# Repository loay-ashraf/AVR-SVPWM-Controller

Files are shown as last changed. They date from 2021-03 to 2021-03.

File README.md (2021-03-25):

# AVR SVPWM Controller
SVPWM controller prototype implemented using AVR 8-bit microcontroller as a part of EV car conversion graduation project for Mechatronics Engineering Bachelor - Fall 2018.

## Overview
This section gives an overview of the system.

### Concept
Space vector pulse width modulation (SVPWM) is an algorithm for the control of pulse width modulation (PWM).

It is used for the creation of alternating current (AC) waveforms; most commonly to drive 3 phase AC powered motors at varying speeds from DC using multiple MOSFET/IGBT transistors. 

### System Layout
System is divided into two separate modules that communicate with each other to acheive the desired output, which are:

#### Pilot Module

Pilot module receives operating parameters from co-pilot (output frequency) and then outputs PWM signals to IGBT bridge, also it checks for current fault signal and in case of current overload it shuts down waiting for a manual reset.

#### Co-Pilot Module

Co-Pilot module reads user input via rotary potentiometer for output frequency, current sensor for current overload signal, then sends operating parameters to Pilot module and finally outputs system status (frequency, RPM, current,...etc.) to a character LCD.

## Discussion
This section discusses desicions made regarding design and implementation.

### Microcontroller

1. We opted for ATmega128 for pilot module as it runs at 16MHZ frequency and also has two 16-bit timers each having three output compare pins.
2. We opted for ATmega32 for co-pilot module as it runs at 16MHZ frequency and has enough pins for interfacing character LCD and current sensors via ADC.

### Communication Protocol

It is found that best communcation type (protocol) for such system would be a parallel communication bus because of the following reasons:

- Distance between modules is so short (<5m)
- Data sent is time senstive
- Pilot module is starving for CPU clock cycles to calculate and update timer's compare registers values and going with parallel would be ideal for this situation as it only costs one CPU clock cycle to read PINx register 

So we opted for an 8-bit wide parallel communication bus (including READY and ACK signals) which would be much faster than any serial communication available (USART, I2C and SPI).

### Timer Mode

We used Phase and Frequency correct PWM mode with ICR1 as TOP value as it mimics the center aligned PWM mode required for the space vector algorithm.

## Sample Output

### Non-Filtered Output

Below is the ouput of the system without attaching low pass LC filter:

SVPWM non-filtered

### Filtered Output

Below is the output of the system with low pass LC filter attached:

SVPWM filtered

## Built With
- Atmel Studio 7 - The official AVR IDE
- AVR-gcc V5.4 - C compiler
- GNU Make - auto-generated makefile
- CadSoft EAGLE - PCB design tool

## Authors
Loay Ashraf - <loay.ashraf.96@gmail.com>

Mohamed Gamal - <muhammed.gamal051@gmail.com>

## License
This project is licensed under the MIT License - see the LICENSE.md file for details

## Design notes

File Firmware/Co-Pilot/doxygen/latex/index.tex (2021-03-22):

\begin{DoxyAuthor}{Author}
Loay Ashraf \href{mailto:loay.ashraf.96@gmail.com}{\tt loay.\+ashraf.\+96@gmail.\+com} 
\end{DoxyAuthor}
\begin{DoxyVersion}{Version}
1.\+0.\+0
\end{DoxyVersion}
This program processes and shows current inverter status like Voltage, Frequency and the speed of the motor and sets the main controller output by communicating via parallel bus using 8-\/bit data line, one A\+CK line and one R\+E\+A\+DY line; It also interfaces 16x2 parallel interface L\+CD.

\begin{DoxyParagraph}{Pin Assignments\+: }

\begin{DoxyItemize}
\item P\+A0\+: Speed Potentiometer signal
\item P\+A1-\/3\+: Phases current signal
\item P\+B0-\/3\+: L\+CD 4-\/bit Data signal
\item P\+B5\+: L\+CD EN signal
\item P\+B6\+: L\+CD RS signal
\item P\+B7\+: Direction Data signal
\item P\+C0-\/7\+: Parallel bus 8-\/bit Data signal
\item P\+D0-\/1\+: Direction Switch signal
\item P\+D3\+: Current Overload signal
\item P\+D5\+: Parallel bus R\+E\+A\+DY signal
\item P\+D6\+: Parallel bus A\+CK signal 
\end{DoxyItemize}
\end{DoxyParagraph}

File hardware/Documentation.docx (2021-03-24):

# T5 pure sine wave inverter

# T5.1 Circuit diagram

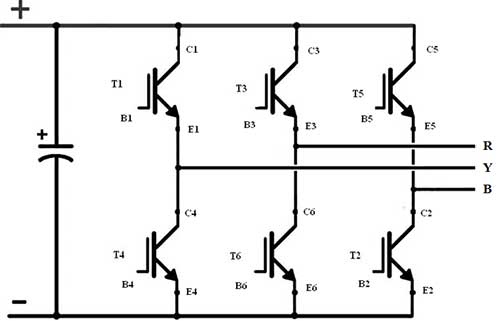
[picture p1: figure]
Description: circuit-diagram-of-three-phase-inverter

The basic circuit of inverter consists of 6 IGBTs connected like this diagram to produce 3-phase system every phase consists of 2 IGBTs each one has phase shift 180 degree which we call for example high side at 0 degree and low side for 180 degree the high side transistor is responsible for generating the positive side of the wave and the low side is responsible for generating the negative side of the wave .Each transistor of the high side has phase shift 120 degree from the next transistor and each transistor of the low side has 120 degree from the next transistor for example: the first phase high side has 0 degree; the second has 120 degree and the 240 degree and the same for low side.

T5.2 Components

T5.2.1 IGBT

The reason of using IGBT neither MOSFET nor BJT isn’t only because the high current and voltage rating but also it has their advantages like high current sensitivity at gate like BJT and high voltage sensitivity at gain like MOSFET.

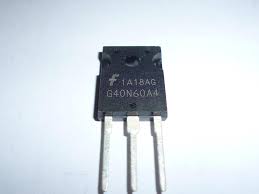
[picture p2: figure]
Description: Image result for igbt g40n60

Fig. IGBT

T5.2.2 Optocoupler driver

The purpose of optocoupler driver is to drive the IGBT gate and isolate the power signal from the control signal in order to protect the power signal from the noise.

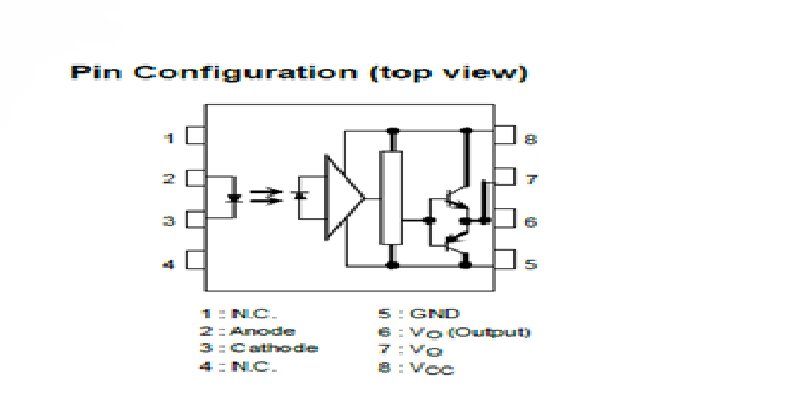
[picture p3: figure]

Fig. optocoupler driver

These are the main components of the main inverter circuit and now let us see the actual inverter circuit you may notice few differences from the basic circuit like the resistors and the capacitors each one has purpose like the 10k ohm resistor between the optocoupler output and the IGBT gate and the 330 ohm at the signal output in the Molex to reduce the amps ,the 10 ohm between the gate and the emitter to prevent parasitic turn on via miller capacitance stray inductance, and the capacitors connected to the driver to work as a filter for the rebels and the noise.

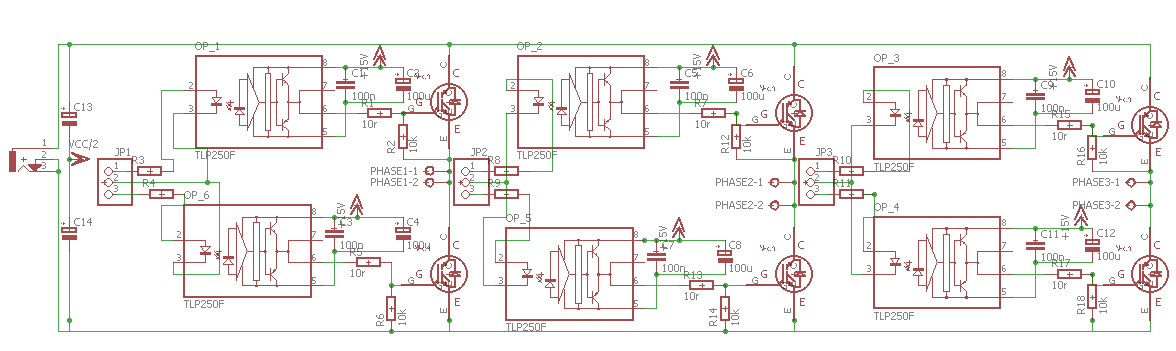
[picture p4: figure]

Fig. The actual inverter circuit

The layout

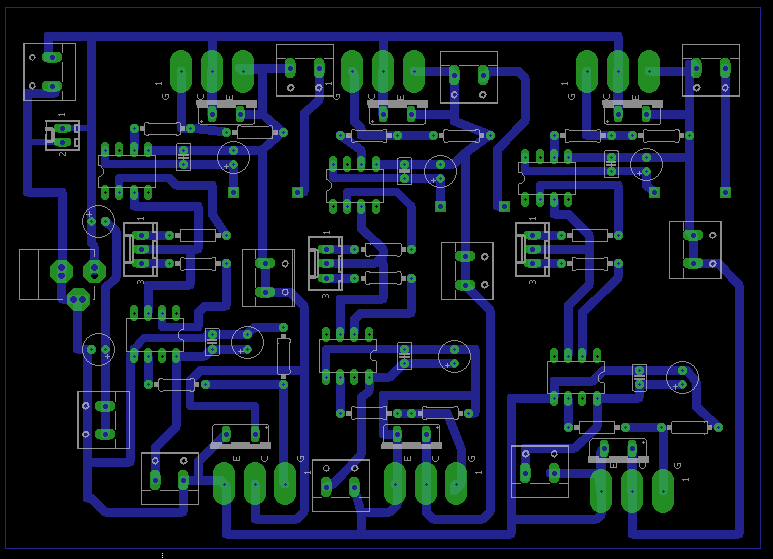
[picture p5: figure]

T5.3 pilot circuit

The pilot circuit is needed to operate and control the inverter output and here the circuit segments in this circuit we used in this circuit ATmega128 because it has two 16-bit timers (Timer1, Timer3), with each timer having 3 output compare units and also can operate in Phase and Frequency Correct (Center-Aligned PWM) mode which is enough for SVPWM signal generation.

T5.3.1 Power supply

The input voltage ranges from 12 to 9 volts the diode is used as a protection method from wrong connection, the 100Uf capacitors are used to reduce the rebels in the supply volt, the 100nF capacitors are used to eliminate the noise from other circuits, the regulator is used to produce 5v from the supply and the led is used as an indicator of the supply.

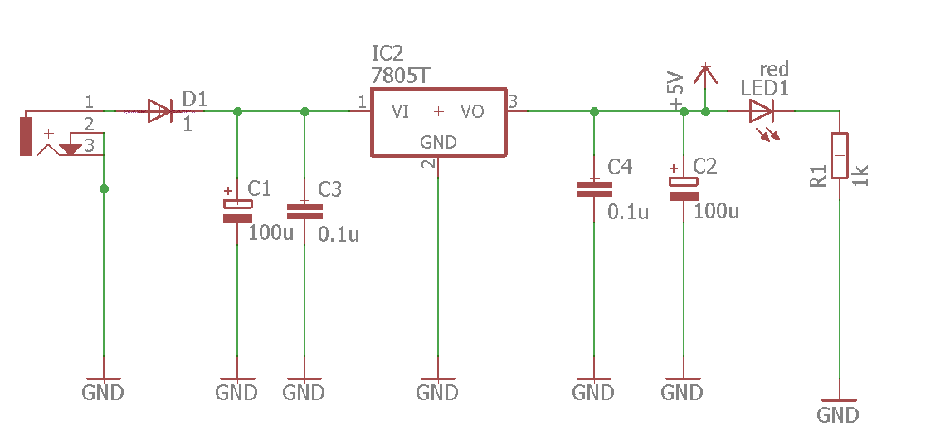
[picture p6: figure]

T5.3.2 Reset circuit

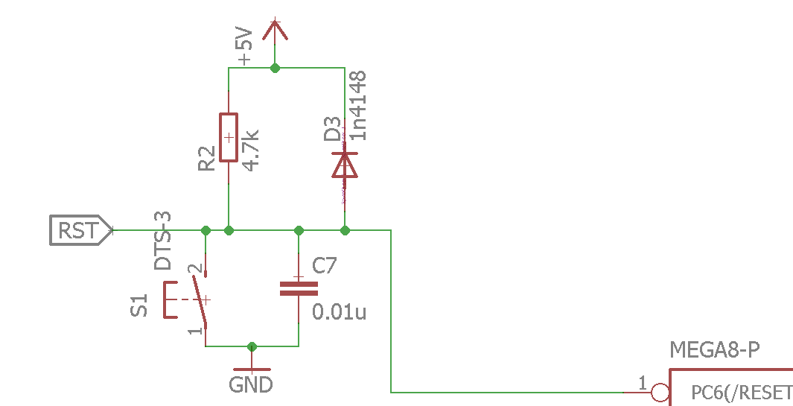
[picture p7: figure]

This circuit is the recommended reset circuit from Atmel.

T5.3.3 Isp programming port

T5.3.4 Logic circuits and Molex

1-not gate

2- Schmitt trigger

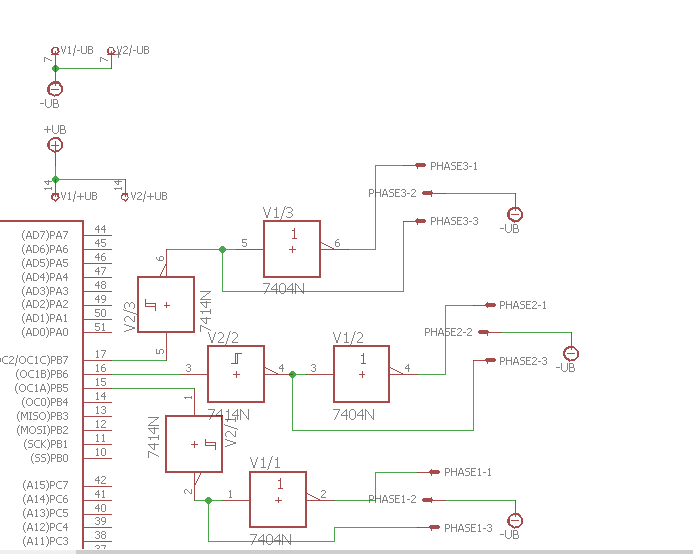
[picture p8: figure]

Fig. Schmitt trigger

The not gate is needed to make the phase shift 180-degree between the high and the low side of each phase the Schmitt trigger is used to make the output increase to a steady max value when the input is between 5v and 2 v and decrease to almost zero when the input is lower than 2, and the 3 pins Molex as output interface between the controller and the inverter circuit.

T5.3.5 Clock circuit

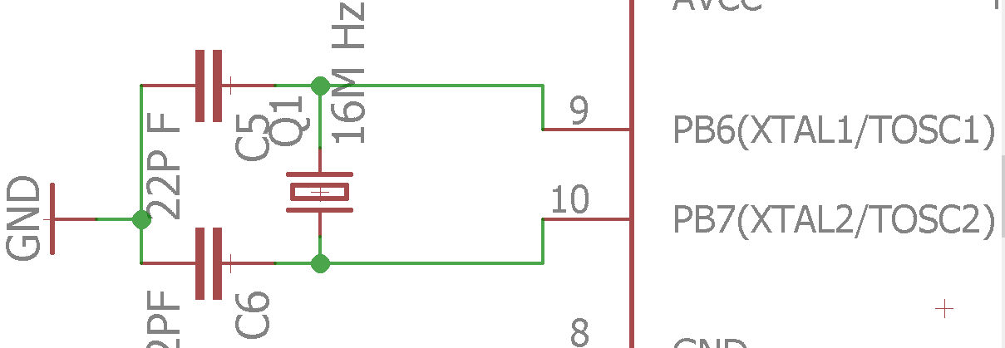
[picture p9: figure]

The 22 pF capacitors are needed to reduce the resonance at the start of the cycle

T5.3.6 Data port

The data port is needed to transfer the data collected from the co-pilot circuit which we need to vary the inverter speed, it consists of 8-bit parallel communication port to receive procced data from the co -pilot, acknowledge as confirmation flag between the co-pilot and the pilot, ready to initiate new data transfer , direction pin which indicates the direction of the motor, RST which is master reset pin between the two controllers and of course the positive and negative rail of the circuit.

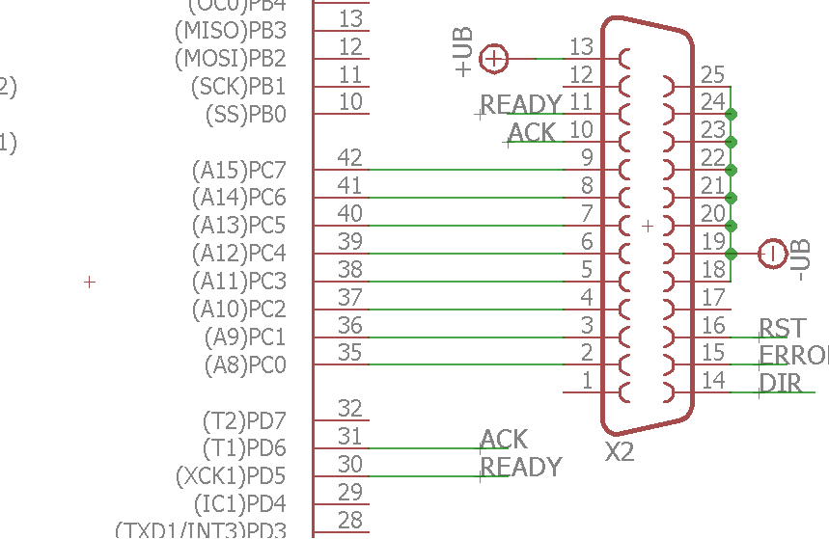
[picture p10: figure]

Full circuit diagram

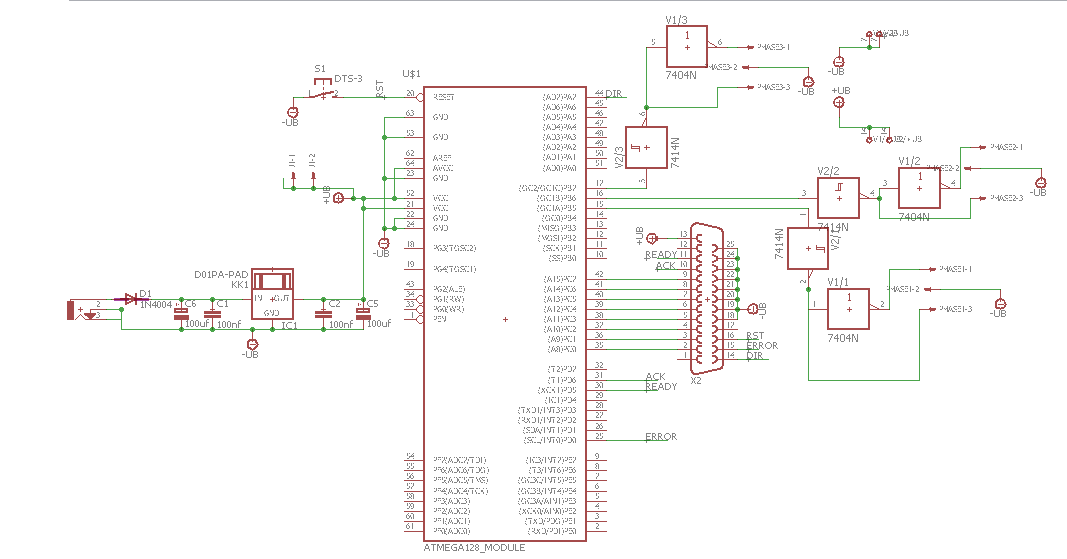
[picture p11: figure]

The layout

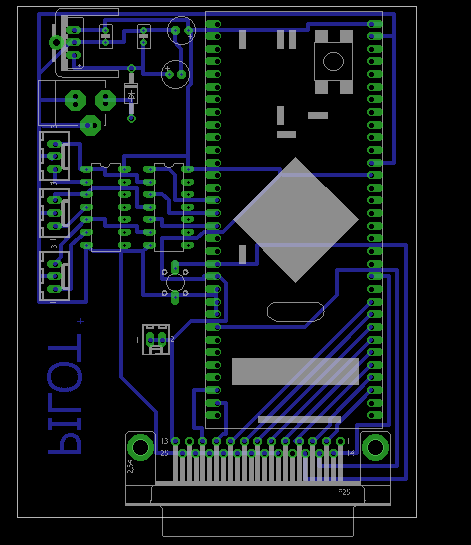
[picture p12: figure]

T5.4 co-pilot circuit

The purpose of the co-pilot circuit is to transform the analog signal from the potentiometer into digital value stored in one single port and display the output of the inverter on LCD for this circuit we have chosen ATmega32 due to presence of large program memory size, SRAM size and number of I/O pins.

1- Clock

The clock circuit is the same like the previous circuit.

2-Data port

The same like the last circuit except that this circuit is the one which transmits the data.

3-Pedals interface

The interface between the circuit and the pedal is 3 pins one; connected to ground, one to V_(cc) and the last one in the middle is connected to ADC pin in microcontroller.

4-Direction interface

We use 3 position switch to display the 3 states of the motor clockwise direction, anti-clockwise direction and stop.

5-LCD Display

We use 16*2-character LCD to display voltage, frequency and speed.

Full circuit diagram

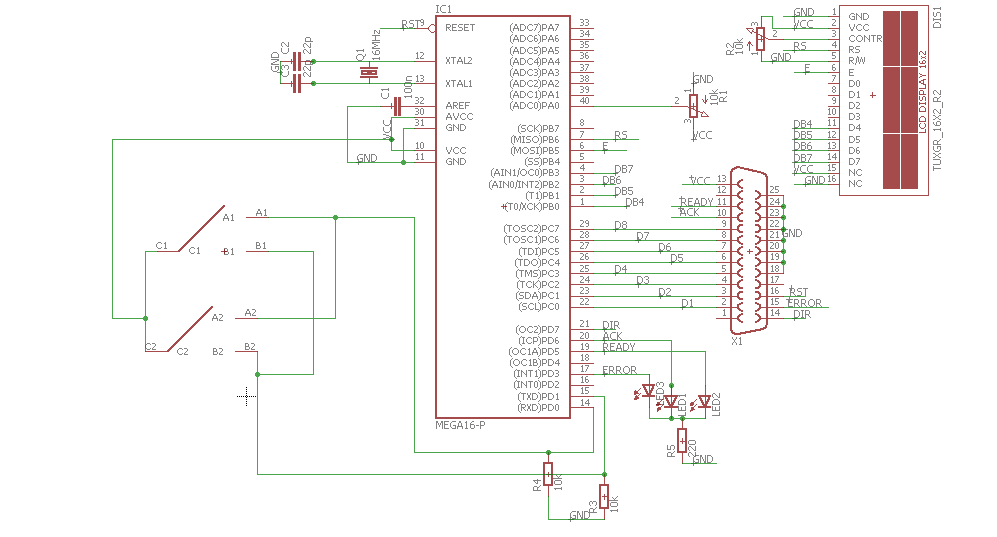
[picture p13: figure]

The layout

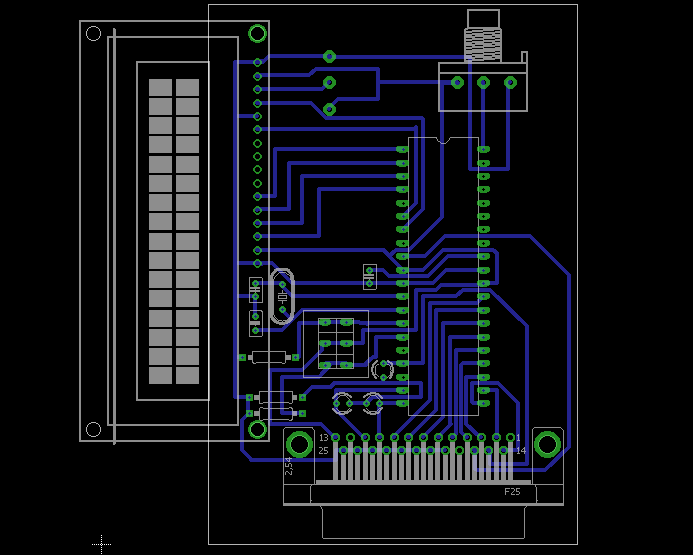
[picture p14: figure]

T5.5 DC filter

We know from the datasheet of the IGBT that the voltage level needed to open the gate is 15 V so the use of dc filter is to reduce the voltage levels difference between sources so the IGBT gates will open simultaneously. We use four dc filters one for the low side transistors and one for each transistor of the high side.

Circuit diagram

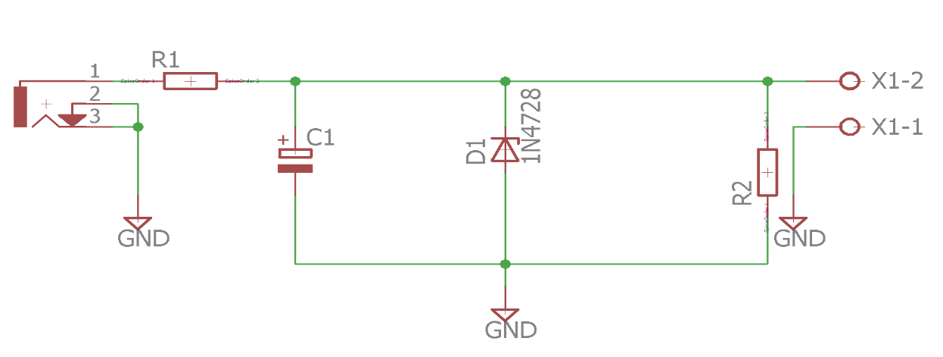
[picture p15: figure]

The layout

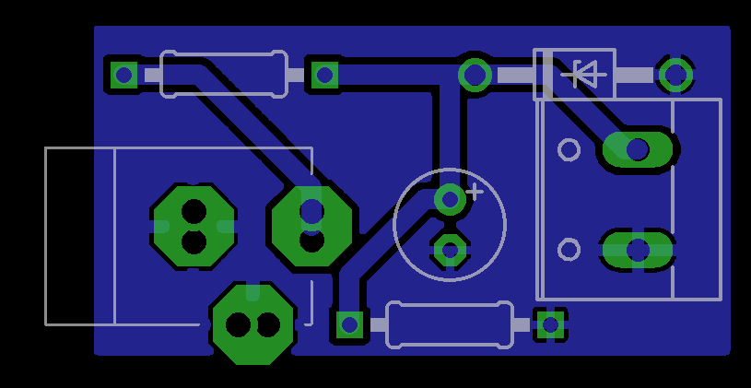
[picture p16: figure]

T5.6 LC Filter circuit

It is known that the output of the inverter is a square wave but we need sinusoidal wave so we need low pass filter circuit like LC filter which consists of inductor reactance and capacitor impulse on the inverter and motor terminals

The values of the capacitor and the inductor is given by

f_c =1/(π√(LC))

Where

f_c is the cut off frequency in hertz

π is mathematical π =3.14

L is the inductance in Henry

C is the capacitance in Farad

For this study case the frequency from the MCU is 7000 HZ

In order to get rid of switching harmonics (up to tenth harmonic)

the cut off frequency of the filter has to be (at most) 700HZ

the available inductance in the market value is 150 u Henry

so, the needed capacitance is 374 u Farad but due to lack of such value in the market we used 8 capacitors each capacitor is 47uFarad for each phase.

Yet such filter will not be able to sustain sine wave shape under every loading condition so a damper circuit is needed.

Circuit diagram

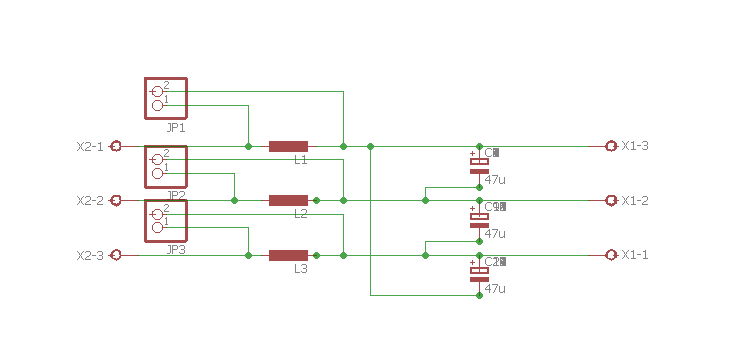
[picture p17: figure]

The layout

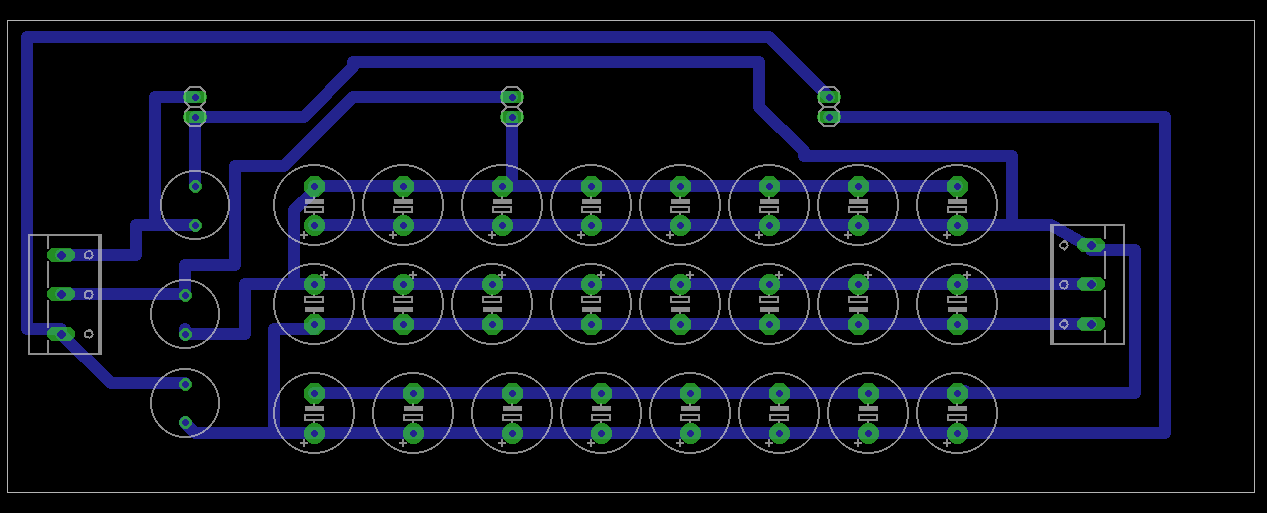
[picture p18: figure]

T5.7 Damper circuit

The presence of dumper eliminates any occasional ringing of output form and helps stabilizes its faster.

There are two kinds of damper

1- series damper:

it consists of a resistor connected in series with inductor and this arrangement is connected parallel with LC filter inductor.

Rd=sqrt(L/C)

Ld=n*L

WHERE n =2/15

2-parallel Damper:

it consists of a resistor connected in series with Capacitor and this arrangement is connected parallel with LC filter Capacitor.

Rd=sqrt(L/C)

Cd=n*C

WHERE n =4

We used in our circuit series damper because the value of the required inductor value is easier to obtain more than the required capacitor in case of parallel damper.

So:

Rd=0.63 ohm

Ld= 20u Henry

Circuit diagram

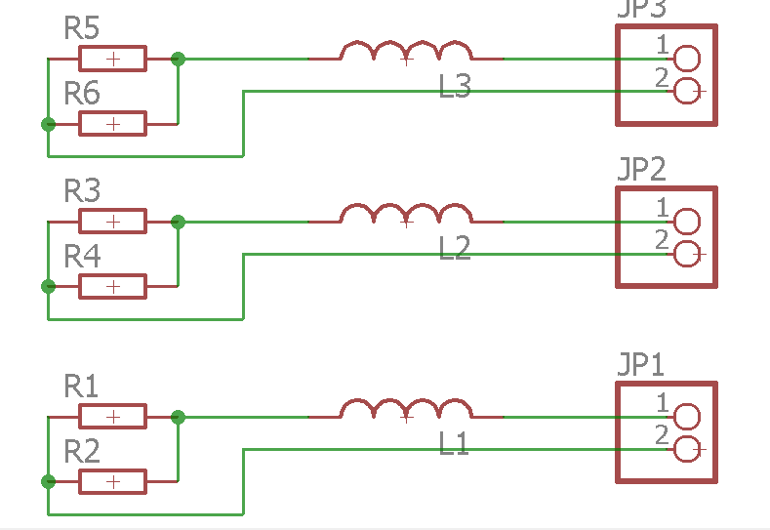
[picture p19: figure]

The layout

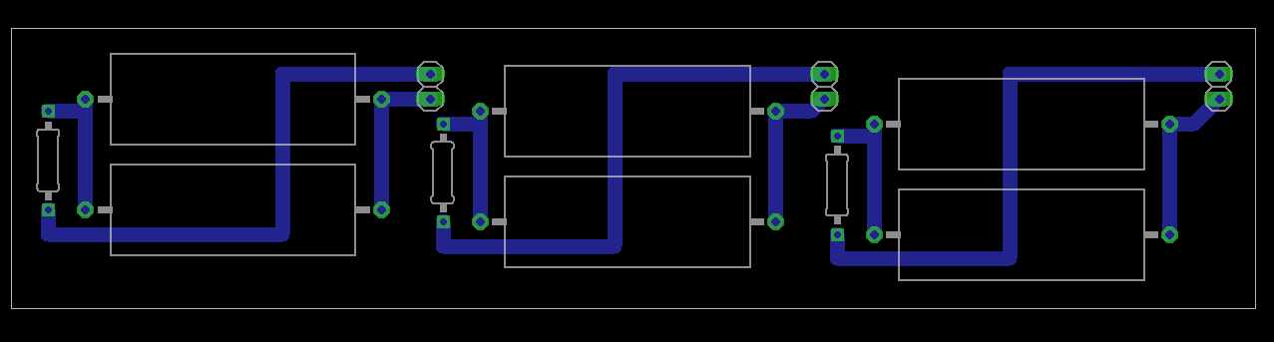
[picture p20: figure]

T6 Excel sheet for inverter calculations

This sheet is used to calculate the amp of the motor as the power and voltage is given &to insert the frequency to be used in further equations.

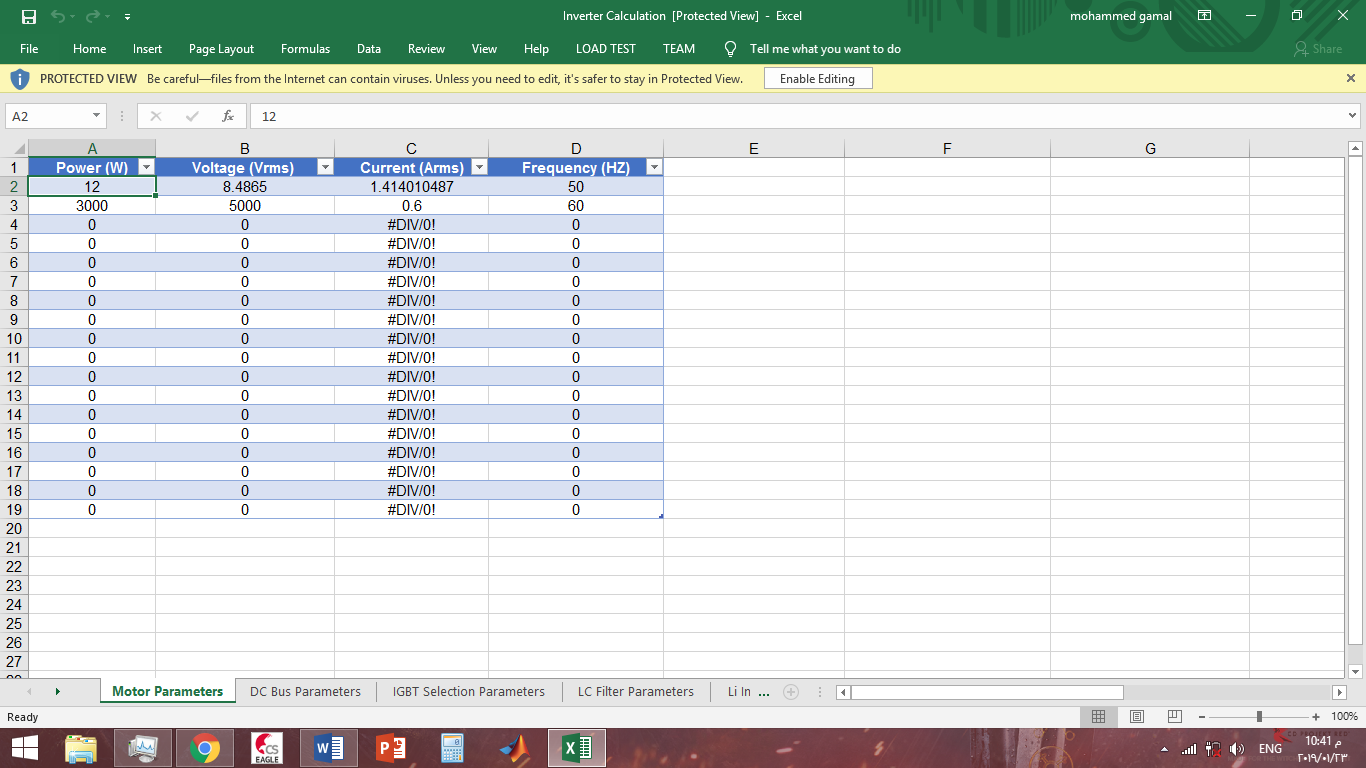
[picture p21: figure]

This sheet is used to calculate both the voltage and amp as rms value

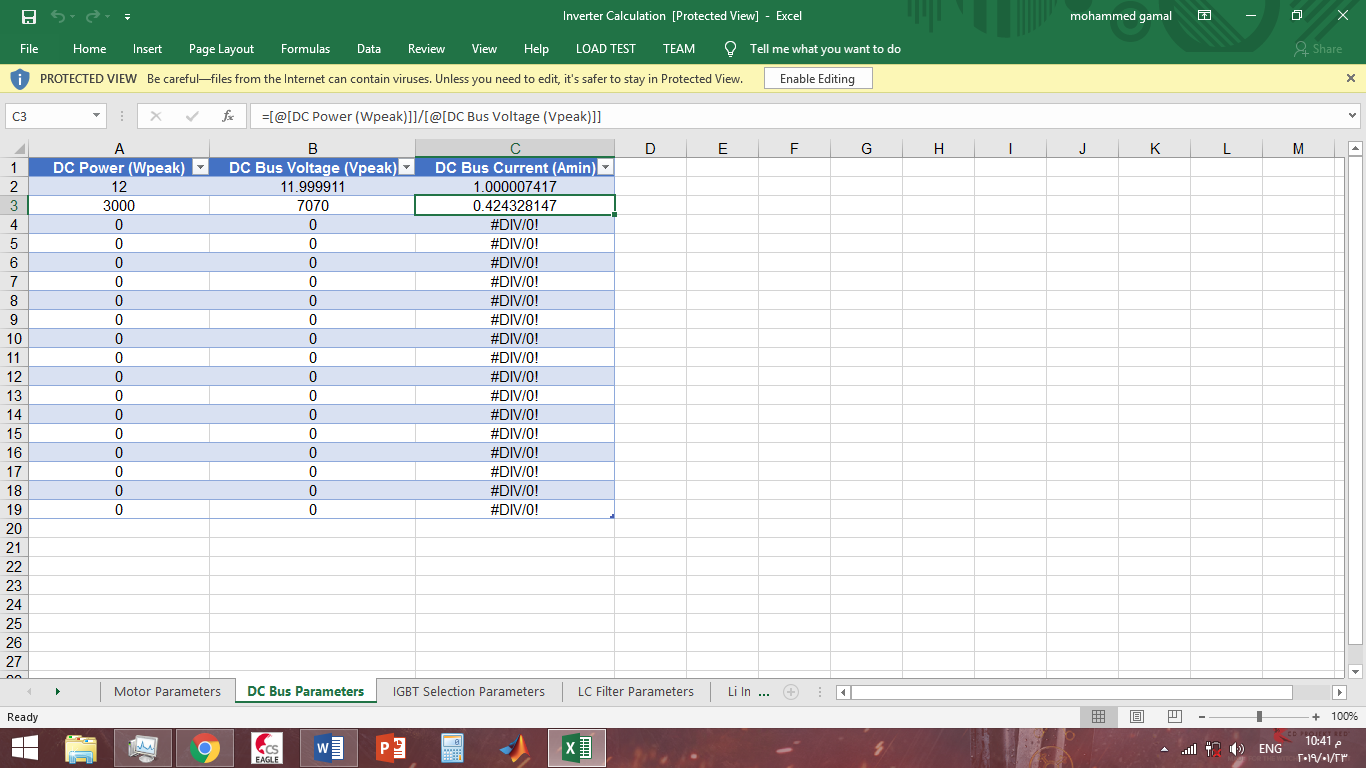
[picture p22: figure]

This sheet to calculate the parameter on which we has chosen the IGBT used in the inverter circuit.

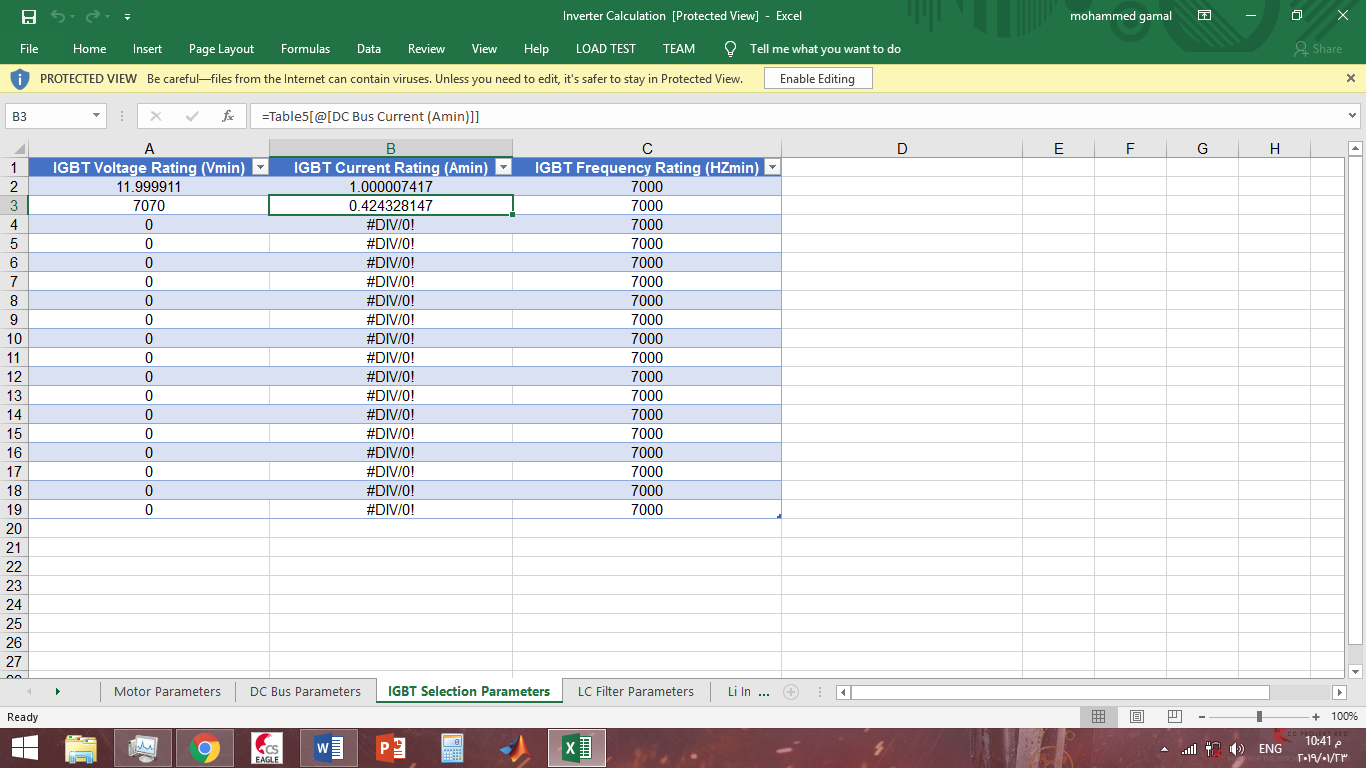
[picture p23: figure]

In this sheet we calculated the parameters of the LC filter and its damper we select reactive power parentage and current ripple due to the application.

This sheet is used to calculate the number of turns for the toroid inductor base on the available core dimensions and the calculated inductance from the previous sheet.

T7 MATLAB simulation

in case of basis inverter, no filter applied

we see that the output is square wave.

in case of inverter with LC filter without the damper

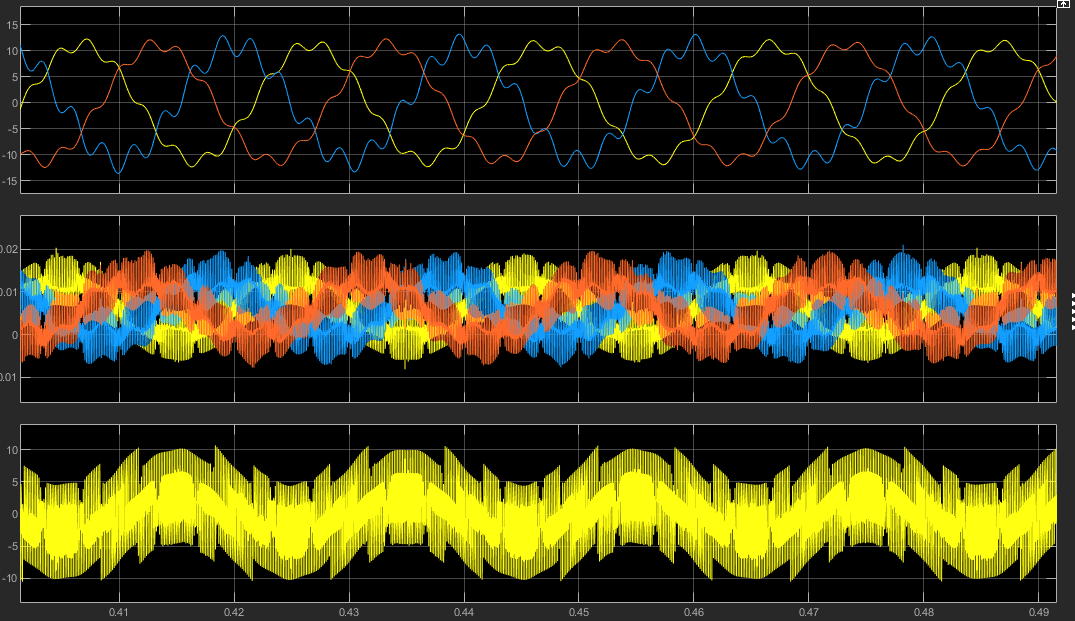
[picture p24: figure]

the wave form takes time to stabilize and even after stabilization the occasional ringing of output form which presents sin wave but with ripples on the peak of the wave.

in case of the inverter with filter and damper

we note the occasional ringing of output form is eliminated and the wave form is stable and presents pure sin wave from the start even on high loads.

T8 the advantages of Pure Sine-wave inverters

-The output waveform is a sine-wave with very low harmonic distortion and clean power like utility supplied electricity

-Inductive loads like microwaves and motors run faster, quieter and cooler

-Reduces audible and electrical noise in fans, fluorescent lights, audio amplifiers, TV, fax and answering machines

-Prevents crashes in computers, weird print outs and glitches in monitors

Electric Vehicle conversion- Graduation Project Mechatronics department, Faculty of Engineering Mansoura University

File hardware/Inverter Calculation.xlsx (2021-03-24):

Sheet: Motor Parameters
Power (W) | Voltage (Vrms) | Current (Arms) | Frequency (HZ)
12 | 8.4865 | 1.414010487 | 50
3000 | 5000 | 0.6 | 60
0 | 0 | #DIV/0! | 0
0 | 0 | #DIV/0! | 0
0 | 0 | #DIV/0! | 0
0 | 0 | #DIV/0! | 0
0 | 0 | #DIV/0! | 0
0 | 0 | #DIV/0! | 0
0 | 0 | #DIV/0! | 0
0 | 0 | #DIV/0! | 0
0 | 0 | #DIV/0! | 0
0 | 0 | #DIV/0! | 0
0 | 0 | #DIV/0! | 0
0 | 0 | #DIV/0! | 0
0 | 0 | #DIV/0! | 0
0 | 0 | #DIV/0! | 0
0 | 0 | #DIV/0! | 0
0 | 0 | #DIV/0! | 0

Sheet: DC Bus Parameters
DC Power (Wpeak) | DC Bus Voltage (Vpeak) | DC Bus Current (Amin)
12 | 11.999911 | 1.000007417
3000 | 7070 | 0.4243281471
0 | 0 | #DIV/0!
0 | 0 | #DIV/0!
0 | 0 | #DIV/0!
0 | 0 | #DIV/0!
0 | 0 | #DIV/0!
0 | 0 | #DIV/0!
0 | 0 | #DIV/0!
0 | 0 | #DIV/0!
0 | 0 | #DIV/0!
0 | 0 | #DIV/0!
0 | 0 | #DIV/0!
0 | 0 | #DIV/0!
0 | 0 | #DIV/0!
0 | 0 | #DIV/0!
0 | 0 | #DIV/0!
0 | 0 | #DIV/0!
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

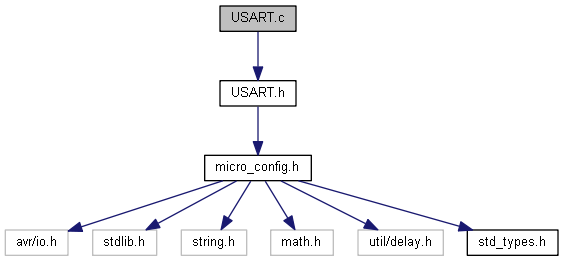
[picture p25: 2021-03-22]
Firmware/Co-Pilot/doxygen/_u_s_a_r_t_8c__incl.png

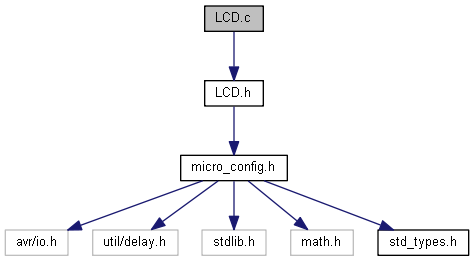
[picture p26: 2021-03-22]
Firmware/Co-Pilot/doxygen/_l_c_d_8c__incl.png

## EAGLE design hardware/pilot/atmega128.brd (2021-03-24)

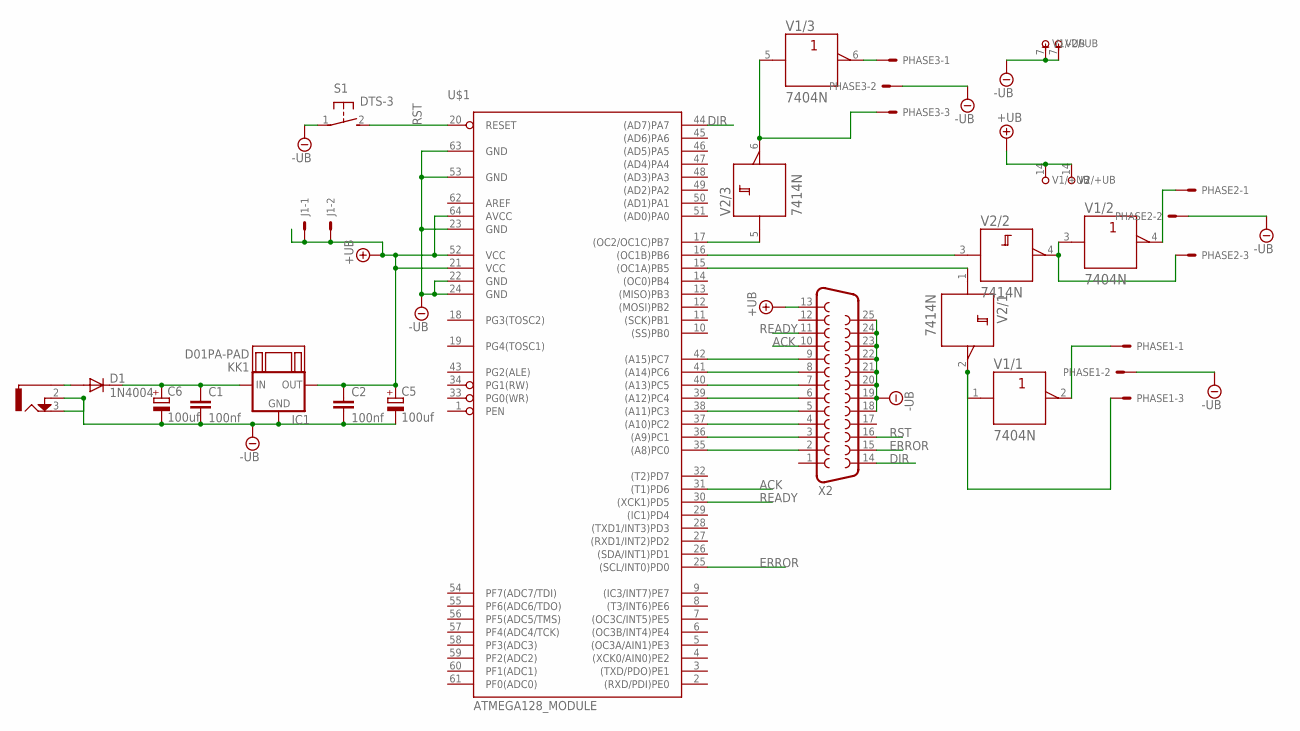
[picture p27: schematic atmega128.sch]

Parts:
C1, C2: 100nf; C025-025X050
C5, C6: 100uf; E2,5-6
D1: 1N4004; DO41-10
IC1: 78XXS
J1: 22-27-2021-02; 6410-02
KK1: D01PA-PAD
PHASE1, PHASE2, PHASE3: 6410-03
S1: DTS-3
U$1: ATMEGA128_MODULE
U$2: DC-21MM
V1: 7404N; DIL14
V2: 7414N; DIL14
X2: F25HP

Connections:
+UB: C2.1, C5.+, IC1.OUT, J1.1, J1.2, U$1.21 (VCC), U$1.52 (VCC), U$1.64 (AVCC), V1.14 (+UB), V2.14 (+UB), X2.13
-UB: C1.2, C2.2, C5.-, C6.-, IC1.GND, PHASE1.2, PHASE2.2, PHASE3.2, S1.1, U$1.22 (GND), U$1.23 (GND), U$1.24 (GND), U$1.53 (GND), U$1.63 (GND), U$2.2, U$2.3, V1.7 (-UB), V2.7 (-UB), X2.18, X2.19, X2.20, X2.21, X2.22, X2.23, X2.24, X2.25
ACK: U$1.31 ((T1)PD6), X2.10
DIR: U$1.44 ((AD7)PA7), X2.14
ERROR: U$1.25 ((SCL/INT0)PD0), X2.15
unnamed: D1.A, U$2.1
unnamed: C1.1, C6.+, D1.C, IC1.IN
unnamed: U$1.42 ((A15)PC7), X2.9
unnamed: U$1.41 ((A14)PC6), X2.8
unnamed: U$1.40 ((A13)PC5), X2.7
unnamed: U$1.39 ((A12)PC4), X2.6
unnamed: U$1.38 ((A11)PC3), X2.5
unnamed: U$1.37 ((A10)PC2), X2.4
unnamed: U$1.36 ((A9)PC1), X2.3
unnamed: U$1.35 ((A8)PC0), X2.2
PHASE1: U$1.15 ((OC1A)PB5), V2.1 (A)
PHASE1HIGH: PHASE1.1, V1.2 (Y)
PHASE1LOW: PHASE1.3, V1.1 (A), V2.2 (Y)
PHASE2: U$1.16 ((OC1B)PB6), V2.3 (A)
PHASE2HIGH: PHASE2.1, V1.4 (Y)
PHASE2LOW: PHASE2.3, V1.3 (A), V2.4 (Y)
PHASE3: U$1.17 ((OC2/OC1C)PB7), V2.5 (A)
PHASE3HIGH: PHASE3.1, V1.6 (Y)
PHASE3LOW: PHASE3.3, V1.5 (A), V2.6 (Y)
READY: U$1.30 ((XCK1)PD5), X2.11
RST: S1.2, U$1.20 (RESET), X2.16

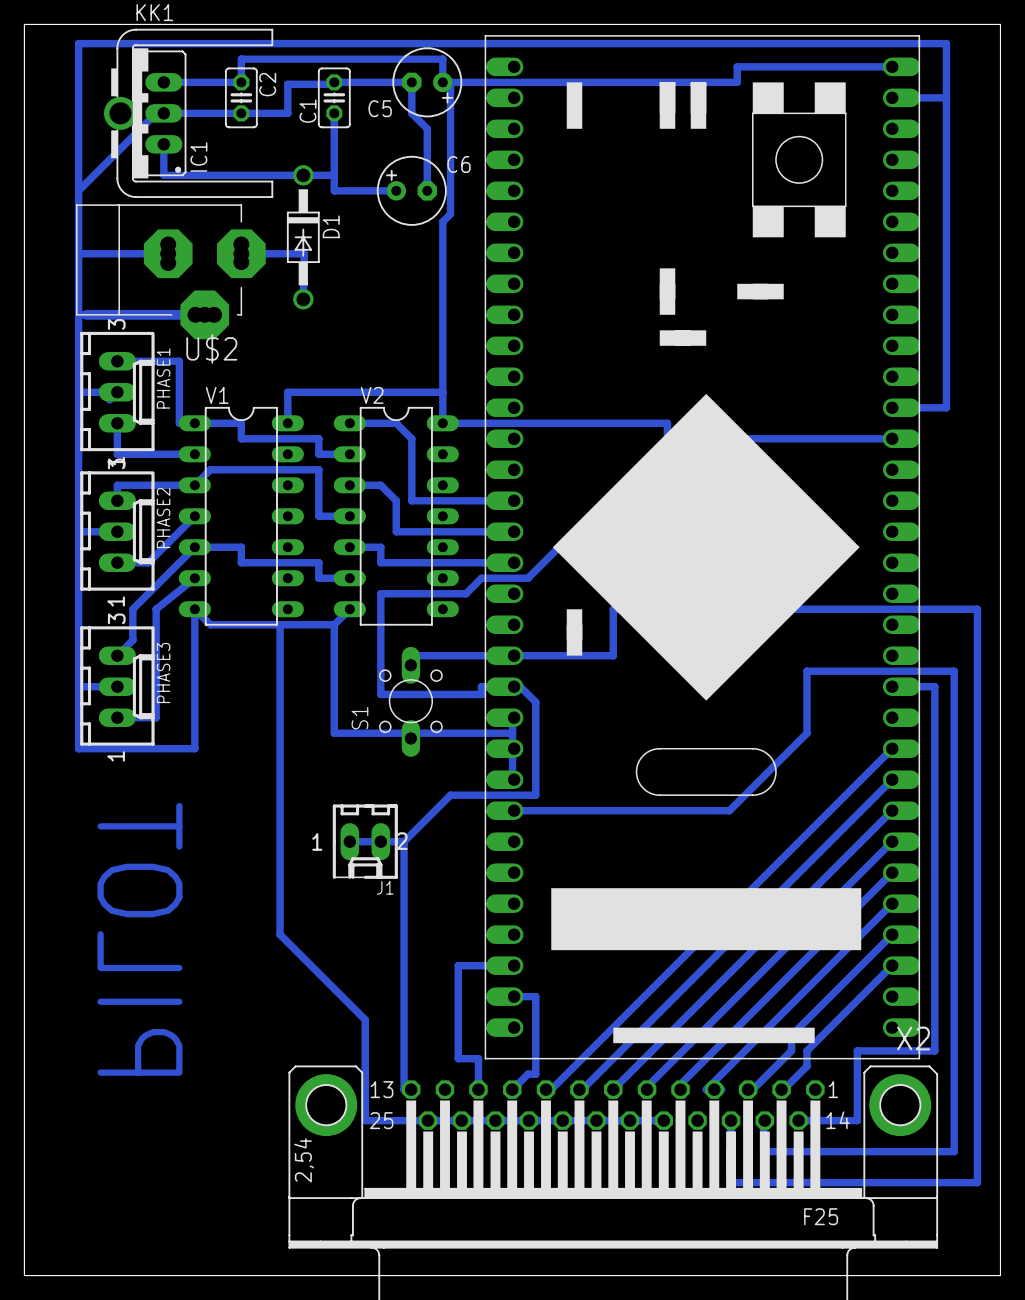
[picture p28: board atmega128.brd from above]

Board: 2 copper layers, 80.0 x 102.5 mm, 17 parts (0 on the bottom side), 26 nets.

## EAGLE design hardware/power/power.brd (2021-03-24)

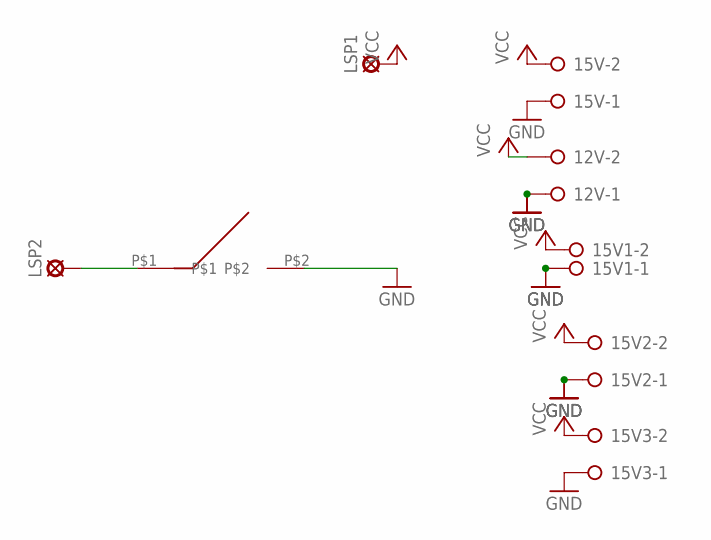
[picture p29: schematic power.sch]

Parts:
12V, 15V, 15V1, 15V2, 15V3: W237-02P; W237-132
LSP1, LSP2: SE14
U$1: ON/OFF

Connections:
GND: 12V.1, 15V.1, 15V1.1, 15V2.1, 15V3.1, U$1.P$2
unnamed: LSP2.MP, U$1.P$1
VCC: 12V.2, 15V.2, 15V1.2, 15V2.2, 15V3.2, LSP1.MP

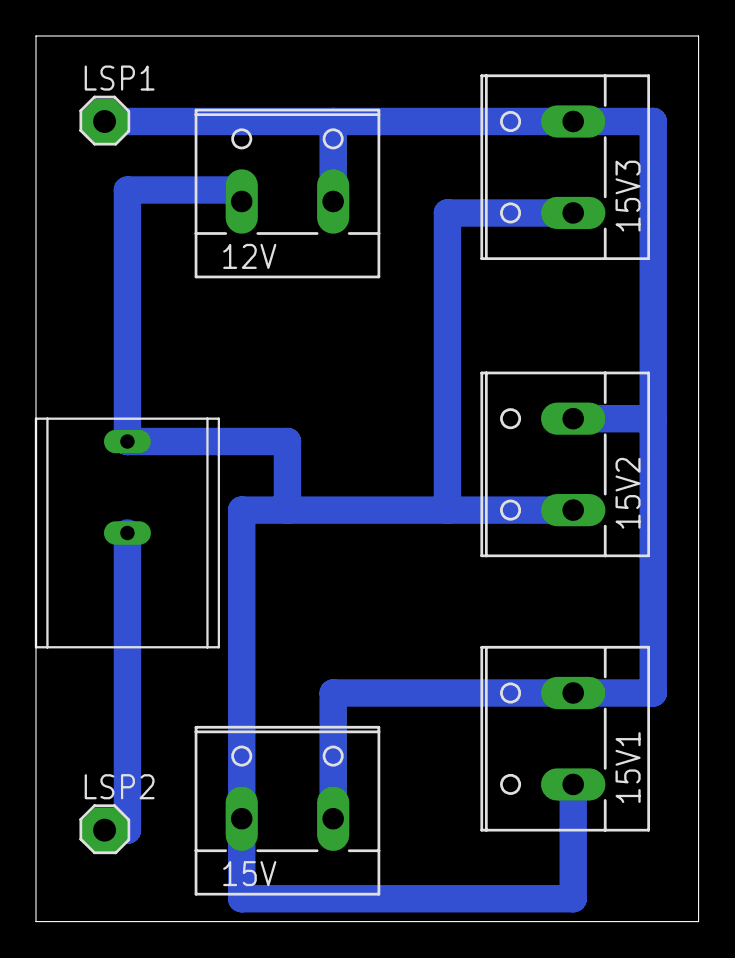
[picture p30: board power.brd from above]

Board: 2 copper layers, 36.8 x 49.2 mm, 8 parts (0 on the bottom side), 3 nets.

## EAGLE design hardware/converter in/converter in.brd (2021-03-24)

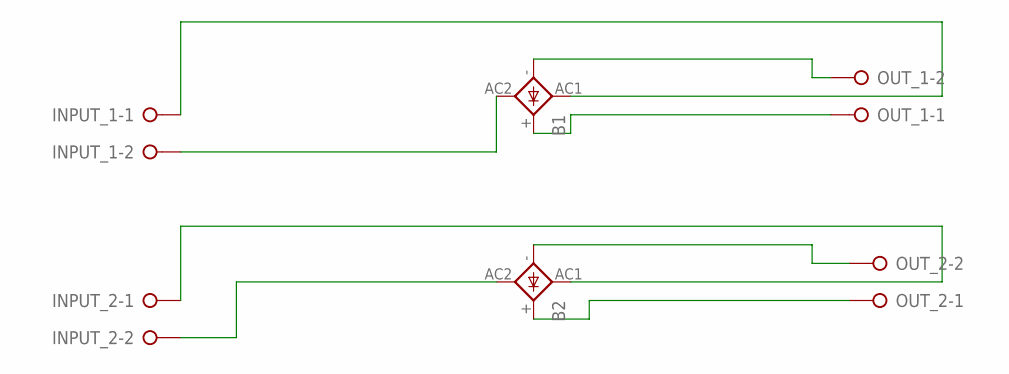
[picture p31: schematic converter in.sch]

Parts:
B1, B2: 2KBP
INPUT_1, INPUT_2: W237-02P; W237-132
OUT_1, OUT_2: W237-02P; W237-132

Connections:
unnamed: B1.-, OUT_1.2
unnamed: B1.+, OUT_1.1
unnamed: B2.-, OUT_2.2
unnamed: B2.+, OUT_2.1
unnamed: B2.AC1, INPUT_2.1
unnamed: B2.AC2, INPUT_2.2
unnamed: B1.AC2, INPUT_1.2
unnamed: B1.AC1, INPUT_1.1

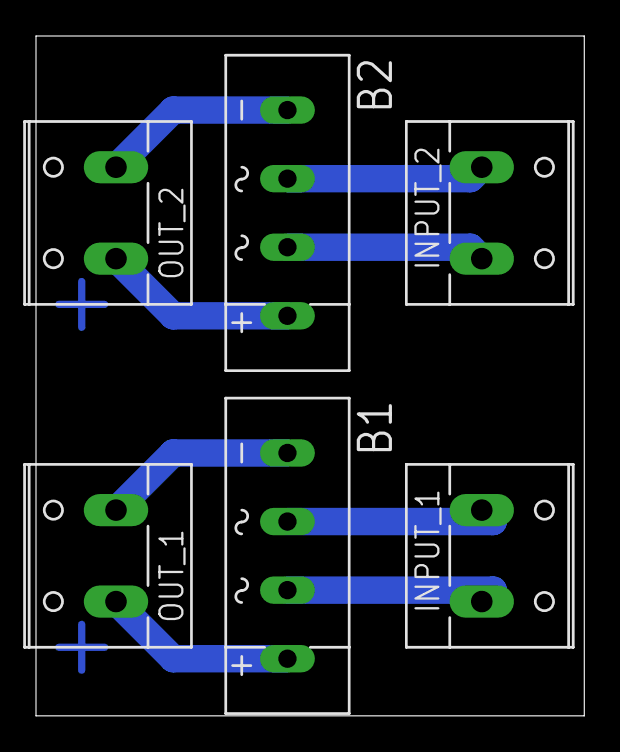
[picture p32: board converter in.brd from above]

Board: 2 copper layers, 30.5 x 37.8 mm, 6 parts (0 on the bottom side), 8 nets.

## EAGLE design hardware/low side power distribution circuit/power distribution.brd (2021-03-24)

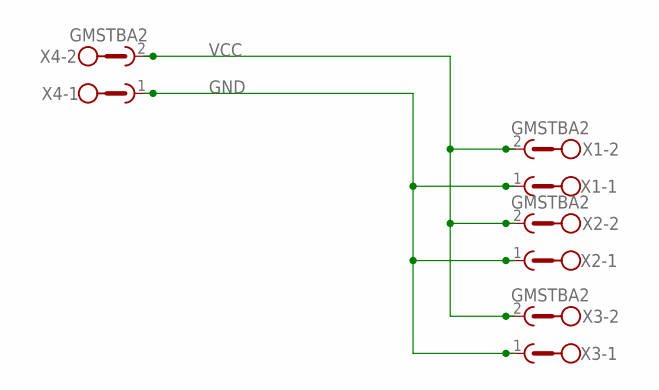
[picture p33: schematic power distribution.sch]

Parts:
X1, X2, X3, X4: GMSTBA2

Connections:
GND: X1.1, X2.1, X3.1, X4.1
VCC: X1.2, X2.2, X3.2, X4.2

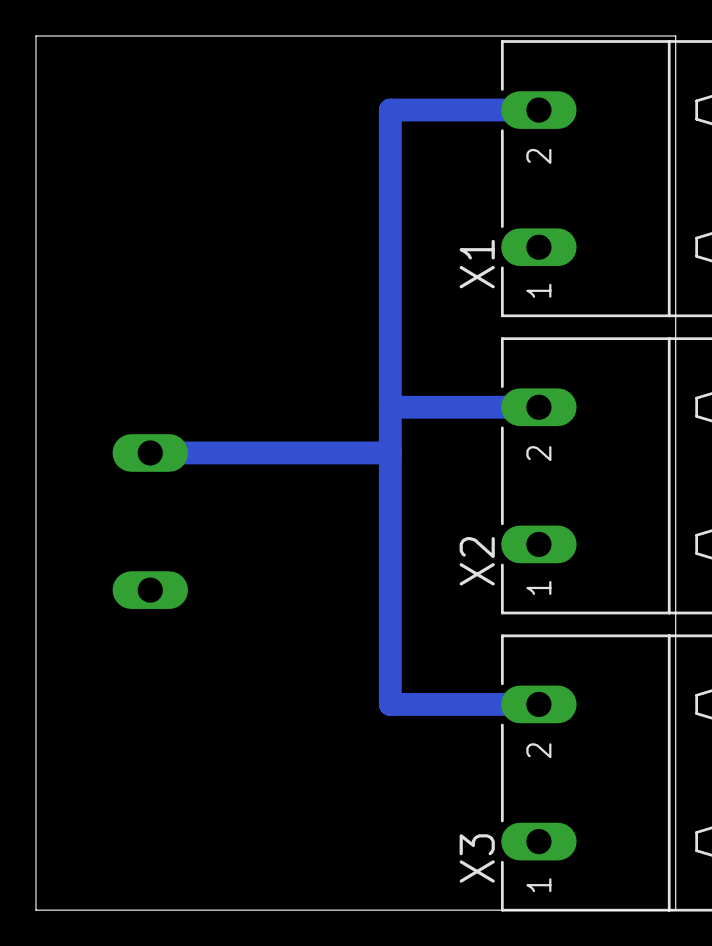
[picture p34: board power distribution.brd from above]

Board: 2 copper layers, 35.5 x 48.6 mm, 4 parts (1 on the bottom side), 2 nets.

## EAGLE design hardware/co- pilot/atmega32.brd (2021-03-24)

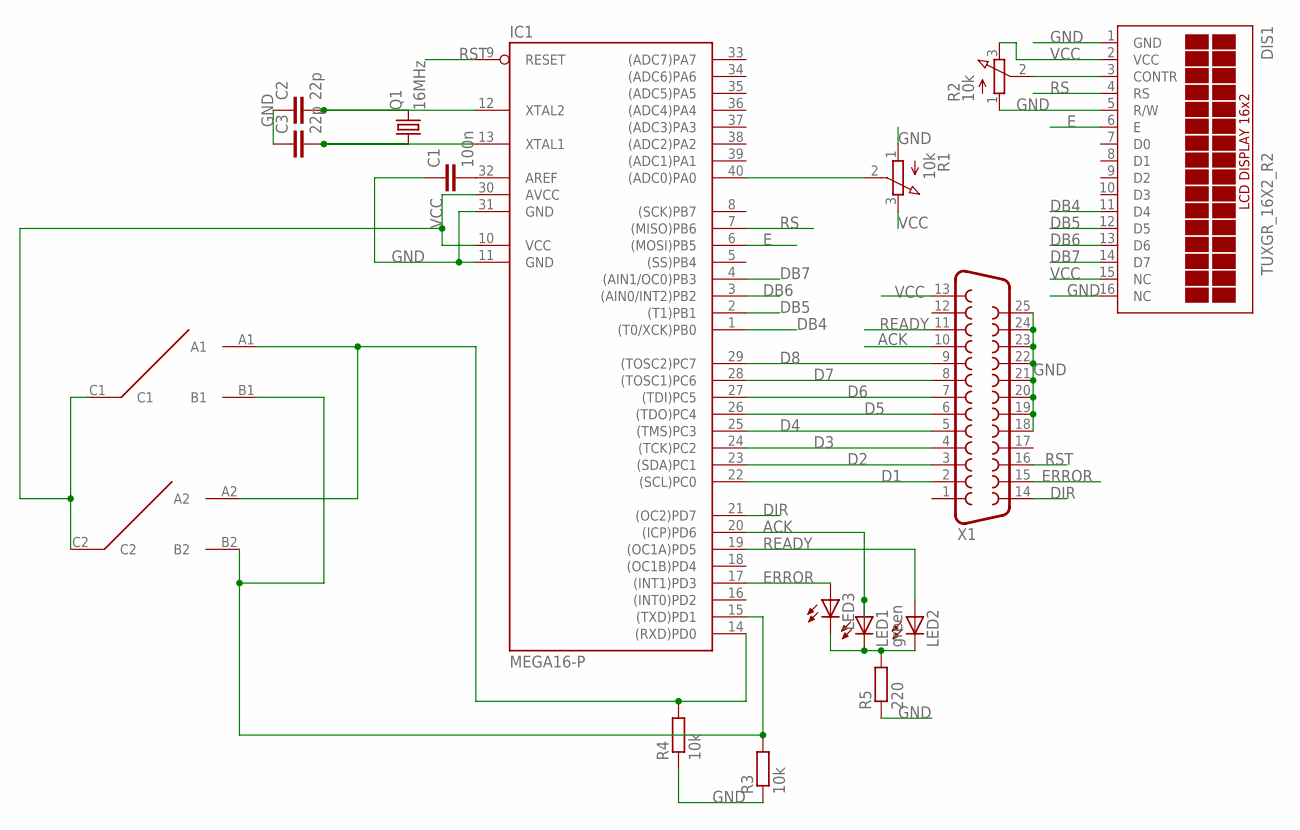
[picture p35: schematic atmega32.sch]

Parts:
C1: 100n; C025-025X050
C2, C3: 22p; C025-025X050
DIS1: TUXGR_16X2_R2
IC1: MEGA16-P; DIL40
LED1: green; LED3MM
LED2, LED3: LED3MM
Q1: 16MHz; HC49/S
R1, R2: 10k; 3RP/1610N
R3, R4: 10k; 0207/10
R5: 220; 0207/10
U$1: TOGGLE
X1: F25HP

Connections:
ACK: IC1.20 ((ICP)PD6), LED1.A, X1.10
D1: IC1.22 ((SCL)PC0), X1.2
D2: IC1.23 ((SDA)PC1), X1.3
D3: IC1.24 ((TCK)PC2), X1.4
D4: IC1.25 ((TMS)PC3), X1.5
D5: IC1.26 ((TDO)PC4), X1.6
D6: IC1.27 ((TDI)PC5), X1.7
D7: IC1.28 ((TOSC1)PC6), X1.8
D8: IC1.29 ((TOSC2)PC7), X1.9
DB4: DIS1.11 (D4), IC1.1 ((T0/XCK)PB0)
DB5: DIS1.12 (D5), IC1.2 ((T1)PB1)
DB6: DIS1.13 (D6), IC1.3 ((AIN0/INT2)PB2)
DB7: DIS1.14 (D7), IC1.4 ((AIN1/OC0)PB3)
DIR: IC1.21 ((OC2)PD7), X1.14
E: DIS1.6 (E), IC1.6 ((MOSI)PB5)
ERROR: IC1.17 ((INT1)PD3), LED3.A, X1.15
GND: C1.1, C2.1, C3.1, DIS1.1 (GND), DIS1.5 (R/W), DIS1.16 (NC), IC1.11 (GND), IC1.31 (GND), R1.1 (A), R2.1 (A), R3.1, R4.1, R5.1, X1.18, X1.19, X1.20, X1.21, X1.22, X1.23, X1.24, X1.25
unnamed: LED1.K (C), LED2.K (C), LED3.K (C), R5.2
unnamed: IC1.14 ((RXD)PD0), R4.2, U$1.A1, U$1.A2
unnamed: IC1.15 ((TXD)PD1), R3.2, U$1.B1, U$1.B2
unnamed: C2.2, IC1.12 (XTAL2), Q1.2
unnamed: IC1.40 ((ADC0)PA0), R1.2 (S)
unnamed: C1.2, IC1.32 (AREF)
unnamed: C3.2, IC1.13 (XTAL1), Q1.1
unnamed: DIS1.3 (CONTR), R2.2 (S)
READY: IC1.19 ((OC1A)PD5), LED2.A, X1.11
RS: DIS1.4 (RS), IC1.7 ((MISO)PB6)
RST: IC1.9 (RESET), X1.16
VCC: DIS1.2 (VCC), DIS1.15 (NC), IC1.10 (VCC), IC1.30 (AVCC), R1.3 (E), R2.3 (E), U$1.C1, U$1.C2, X1.13

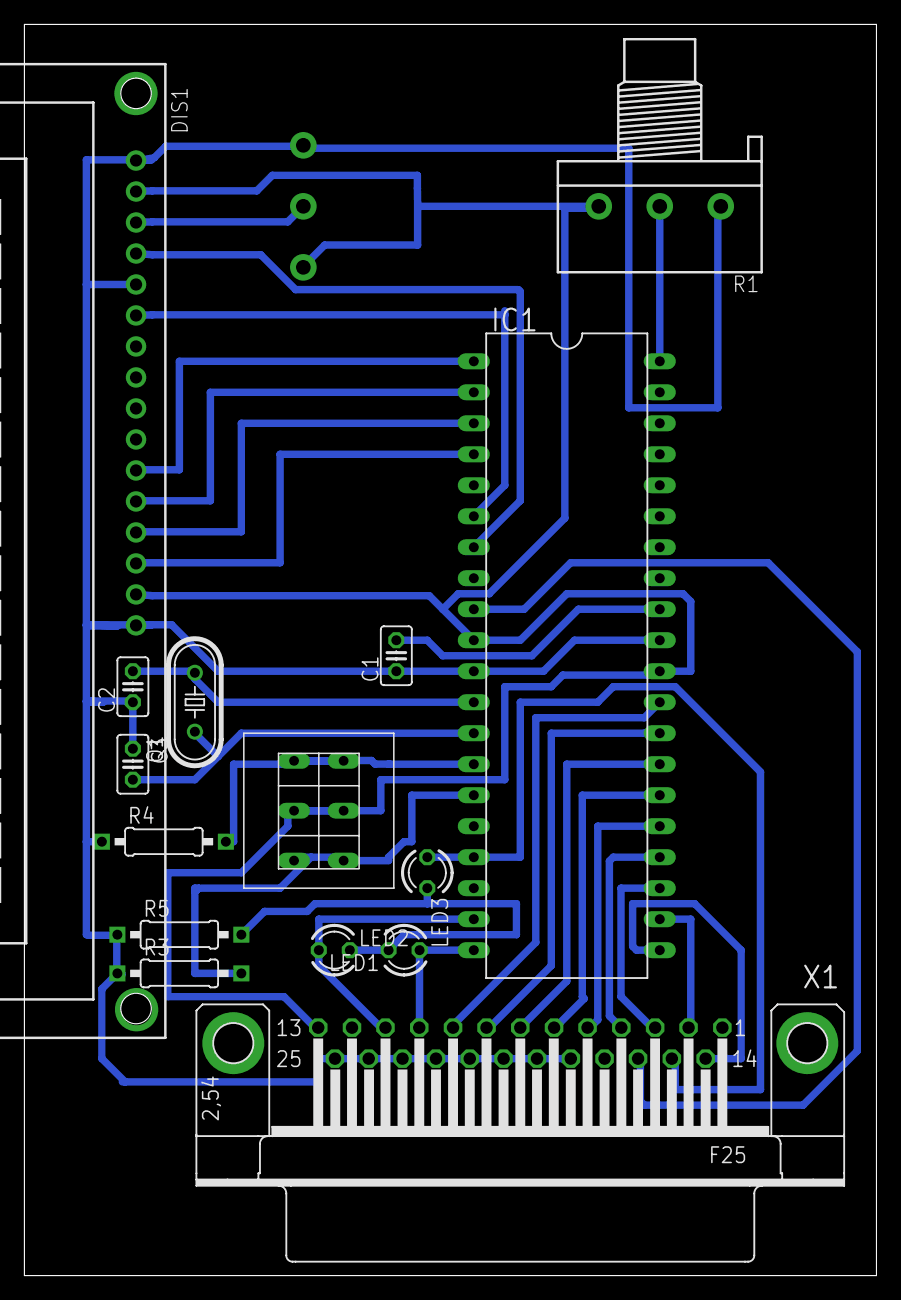
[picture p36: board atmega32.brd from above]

Board: 2 copper layers, 69.8 x 102.5 mm, 16 parts (1 on the bottom side), 29 nets.

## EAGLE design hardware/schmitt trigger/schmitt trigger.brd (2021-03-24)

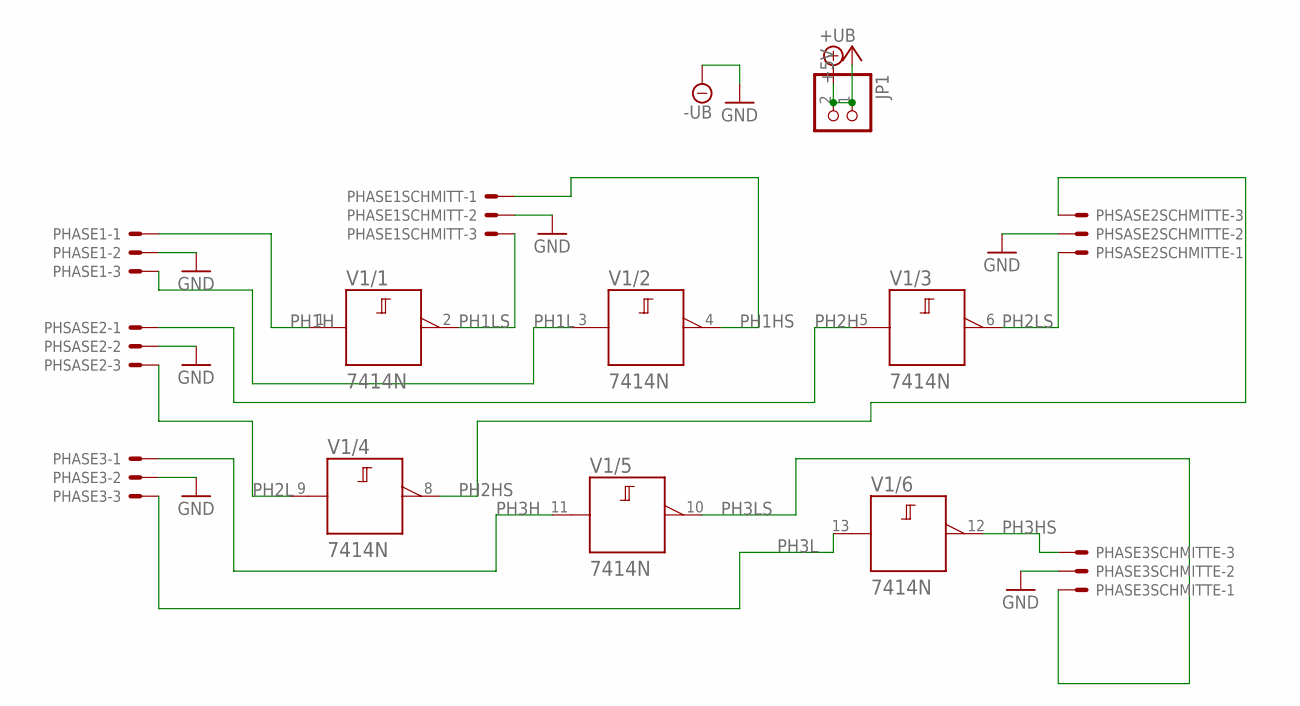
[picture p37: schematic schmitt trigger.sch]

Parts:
JP1: PINHD-1X2; 1X02
PHASE1, PHASE1SCHMITT, PHASE3, PHASE3SCHMITTE: 22-23-2031
PHSASE2, PHSASE2SCHMITTE: 22-23-2031
V1: 7414N; DIL14

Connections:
+5V: JP1.1, JP1.2, V1.14 (+UB)
GND: PHASE1.2, PHASE1SCHMITT.2, PHASE3.2, PHASE3SCHMITTE.2, PHSASE2.2, PHSASE2SCHMITTE.2, V1.7 (-UB)
PH1H: PHASE1.1, V1.1 (A)
PH1HS: PHASE1SCHMITT.1, V1.4 (Y)
PH1L: PHASE1.3, V1.3 (A)
PH1LS: PHASE1SCHMITT.3, V1.2 (Y)
PH2H: PHSASE2.1, V1.5 (A)
PH2HS: PHSASE2SCHMITTE.3, V1.8 (Y)
PH2L: PHSASE2.3, V1.9 (A)
PH2LS: PHSASE2SCHMITTE.1, V1.6 (Y)
PH3H: PHASE3.1, V1.11 (A)
PH3HS: PHASE3SCHMITTE.3, V1.12 (Y)
PH3L: PHASE3.3, V1.13 (A)
PH3LS: PHASE3SCHMITTE.1, V1.10 (Y)

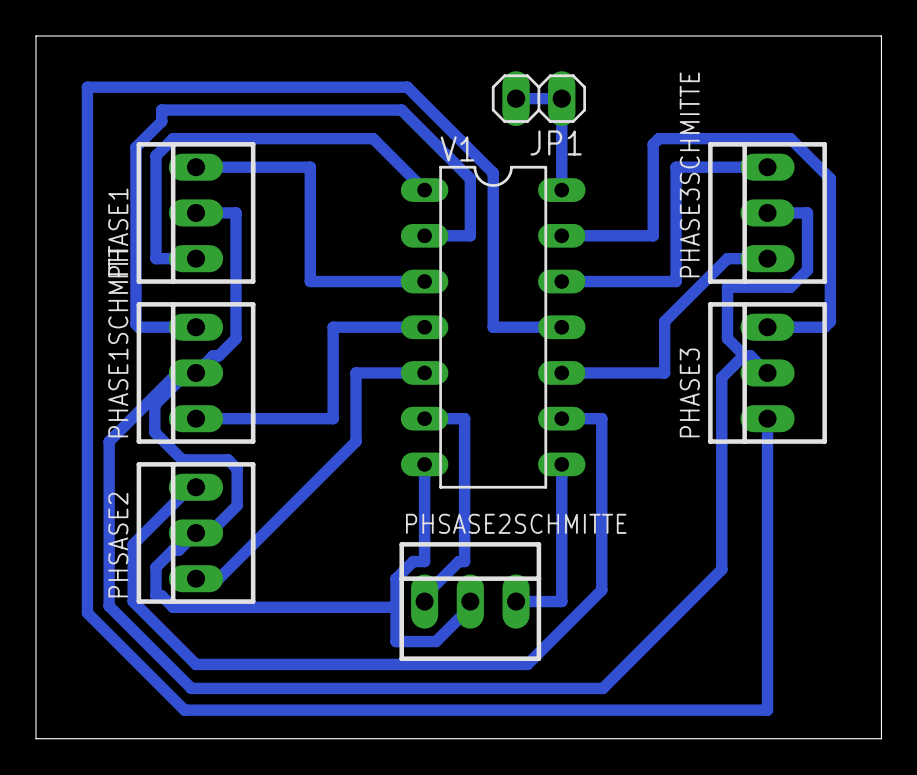
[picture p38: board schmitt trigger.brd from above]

Board: 2 copper layers, 47.0 x 39.0 mm, 8 parts (0 on the bottom side), 14 nets.

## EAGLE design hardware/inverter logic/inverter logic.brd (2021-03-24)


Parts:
C1, C3, C5, C7, C9, C11: 100n; C025-025X050
C2, C4, C6, C8, C10, C12: 100u; E2,5-6
C13, C14: CPOL-EUE2.5-6; E2,5-6
D1, D2, D3, D4, D5, D6: BYW29; DO220S
DRIVE_LOW, DRIVE_LOW1, DRIVE_LOW2: W237-02P; W237-132
DRIVE_SOURCE1, DRIVE_SOURCE2, DRIVE_SOURCE3: W237-02P; W237-132
J1: 22-27-2021-02; 6410-02
OP_1, OP_2, OP_3, OP_4, OP_5, OP_6: TLP250F; DIL08
PHASE1, PHASE2: 22-27-2031-03; 6410-03
PHSASE3: 22-27-2031-03; 6410-03
POWER: W237-02P; W237-132
R1, R3, R5, R7, R9, R11: 10R; 0207/10
R2, R4, R6, R8, R10, R12: 10K; 0207/10
RH1, RH2, RH3: 330; 0207/10
RL1, RL2, RL3: 330; 0207/10
T1, T2, T3, T4, T5, T6: TO-247A; TO-247
U$1: DC-21MM
X1, X2, X3, X4: W237-02P; W237-132

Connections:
+15V: C7.1, C8.+, C9.1, C10.+, C11.1, C12.+, DRIVE_LOW.1, DRIVE_LOW1.1, DRIVE_LOW2.1, OP_4.8 (VCC), OP_5.8 (VCC), OP_6.8 (VCC)
+15V1: C1.1, C2.+, DRIVE_SOURCE1.1, OP_1.8 (VCC)
+15V2: C3.1, C4.+, DRIVE_SOURCE2.1, OP_2.8 (VCC)
+15V3: C5.1, C6.+, DRIVE_SOURCE3.1, OP_3.8 (VCC)
CTRL_GND: OP_1.3 (K), OP_2.3 (K), OP_3.3 (K), OP_4.3 (K), OP_5.3 (K), OP_6.3 (K), PHASE1.2, PHASE2.2, PHSASE3.2
G1: R1.2, R2.2, T1.G
G2: R3.2, R4.2, T2.G
G3: R5.2, R6.2, T3.G
G4: R7.2, R8.2, T4.G
G5: R9.2, R10.2, T5.G
G6: R11.2, R12.2, T6.G
N: C13.-, C14.+, X4.1, X4.2
unnamed: PHASE1.3, RL1.1
unnamed: PHASE2.3, RL2.1
unnamed: PHSASE3.3, RL3.1
unnamed: PHASE2.1, RH2.1
unnamed: PHSASE3.1, RH3.1
unnamed: OP_3.6 (VO), R5.1
unnamed: PHASE1.1, RH1.1
unnamed: OP_1.6 (VO), R1.1
unnamed: OP_2.6 (VO), R3.1
unnamed: OP_4.6 (VO), R7.1
unnamed: OP_5.6 (VO), R9.1
unnamed: OP_6.6 (VO), R11.1
PHASE1: C1.2, C2.-, D1.A, D4.C, DRIVE_SOURCE1.2, OP_1.5 (GND), R2.1, T1.E, T4.C, X1.1, X1.2
PHASE2: C3.2, C4.-, D2.A, D5.C, DRIVE_SOURCE2.2, OP_2.5 (GND), R4.1, T2.E, T5.C, X2.1, X2.2
PHASE3: C5.2, C6.-, D3.A, D6.C, DRIVE_SOURCE3.2, OP_3.5 (GND), R6.1, T3.E, T6.C, X3.1, X3.2
POWER: C13.+, D1.C, D2.C, D3.C, J1.1, POWER.2, T1.C, T2.C, T3.C, U$1.1
POWER_GND: C7.2, C8.-, C9.2, C10.-, C11.2, C12.-, C14.-, D4.A, D5.A, D6.A, DRIVE_LOW.2, DRIVE_LOW1.2, DRIVE_LOW2.2, J1.2, OP_4.5 (GND), OP_5.5 (GND), OP_6.5 (GND), POWER.1, R8.1, R10.1, R12.1, T4.E, T5.E, T6.E, U$1.2, U$1.3
SIGNAL_HIGH1: OP_1.2 (A), RH1.2
SIGNAL_HIGH2: OP_2.2 (A), RH2.2
SIGNAL_HIGH3: OP_3.2 (A), RH3.2
SIGNAL_LOW1: OP_4.2 (A), RL1.2
SIGNAL_LOW2: OP_5.2 (A), RL2.2
SIGNAL_LOW3: OP_6.2 (A), RL3.2


Board: 2 copper layers, 134.6 x 96.2 mm, 66 parts (0 on the bottom side), 35 nets.

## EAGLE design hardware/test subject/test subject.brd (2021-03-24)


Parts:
LED1, LED2, LED3, LED4, LED5, LED6: LED5MM
PHASE2: 22-27-2031-03; 6410-03
PHASE_1: 22-27-2031-03; 6410-03
PHSAE3: 22-27-2031-03; 6410-03

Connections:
unnamed: LED1.A, PHASE_1.3
unnamed: LED4.A, PHASE_1.1
unnamed: LED5.A, PHASE2.1
unnamed: LED2.A, PHASE2.3
unnamed: LED6.A, PHSAE3.1
unnamed: LED3.A, PHSAE3.3
unnamed: LED1.K (C), LED4.K (C), PHASE_1.2
unnamed: LED2.K (C), LED5.K (C), PHASE2.2
unnamed: LED3.K (C), LED6.K (C), PHSAE3.2


Board: 2 copper layers, 53.3 x 16.2 mm, 9 parts (0 on the bottom side), 9 nets.

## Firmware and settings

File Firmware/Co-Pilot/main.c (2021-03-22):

/** @mainpage About
 *  @author Loay Ashraf <loay.ashraf.96@gmail.com>
 *  @version 1.0.0 
 *
 *  This program is implemented on ATmega16/32 running 
 *	at 16 MHZ CPU clock; it basically processes and shows 
 *	current inverter status like Voltage, Frequency 
 *  and the speed of the motor and sets the main controller 
 *	output by communicating via parallel bus using 8-bit 
 *	data line, one ACK line and one READY line; It also 
 *	interfaces 16x2 parallel interface character LCD 
 *	as an output. 
 *	
 *	@pinassignments	
 *	
 *	- PA0: Speed Potentiometer signal
 *	- PA1-3: Phases current signal
 *	- PB0-3: LCD 4-bit Data signal
 *	- PB5: LCD EN signal
 *	- PB6: LCD RS signal
 *	- PB7: Direction Data signal
 *	- PC0-7: Parallel bus 8-bit Data signal
 *	- PD0-1: Direction Switch signal
 *	- PD3: Current Overload ERROR signal
 *	- PD5: Parallel bus READY signal
 *	- PD6: Parallel bus ACK signal	
 *  
 *	@see main.c
 */


/** @file main.c
 *  @brief includes the main function
 *  
 *  the main function acquires data like set Voltage, Phases current,
 *	Direction, etc.; and it sends that data to the LCD and the main 
 *	controller over the parallel bus and sends an ERROR signal if any
 *	current overload happens for any of the 3 phases.
 *
 *  @author Loay Ashraf
 *	@version 1.0.0
 *  @pre include ADC.h, LCD.h, math.h and set F_CPU in micro_config.h
 *  @bug no known bugs
 *  @see micro_config.h
 */

//------------INCLUDE DEVICE DRIVERS------------//

#include "ADC.h"
#include "LCD.h"

//------------DEFINE DATA CALCULATION PARAMETERS------------//

#define VF_SLOPE 0.13333
#define MAX_VOLT 12
#define MIN_VOLT 0.2
#define AMMETER_VOLT 0.35 
#define RESISTOR_VALUE 1
#define CURRENT_THRESHOLD 2

//------------DECLARE GLOBAL VARIABLES------------//

/** @var float Volt
 *  @brief Stores current set Volt value
 */

/** @var float prev_Volt
 *  @brief Stores previous set Volt value to check for change
 */

 /** @var float Freq
 *  @brief Stores current commutation frequency
 */
 
 /** @var float C_PHa
 *  @brief Stores current Phase A current value
 */
 
 /** @var float C_PHb
 *  @brief Stores current Phase B current value
 */
 
 /** @var float C_PHc
 *  @brief Stores current Phase C current value
 */
 
 /** @var uint8 ACK_Flag
 *  @brief Stores previous ACK value to check for change
 */
float Volt, prev_Volt, Freq, C_PHa, C_PHb, C_PHc; 
uint8 ACK_Flag;

/** @brief the main function
 *
 *  see main.c description
 *
 *  @return exit status (1 or 0)
 */
int main(void){
    
	//------------INITIALIZE I/O PORTS------------//
	
	DDRA = 0x00;	// ADC PORT	
	DDRB = 0xFF;	// LCD DATA PORT
	DDRC = 0xFF;	// PARALLEL DATA PORT
	DDRD = 0x28;	// DIRECTION SW AND ACK/READY/FAULT PORT
	
	//------------INITIALIZE ADC AND LCD------------//
	
	ADC_Init(AVCC, RIGHT_ADJ, 128);	// AVCC as Vref, right sdjuted result (10-bit), 128 prescaler
	ADC_Read(ADC0);
	ADC_Read(ADC1);
	ADC_Read(ADC2);
	ADC_Read(ADC3);
	LCD_init(BO, BO);
	LCD_set_cursor(0,4);
	LCD_write_string("Stopped");

    while (1){
		
		//------------ACQUIRE CURRENT ACK STATUS AND DATA VIA ADC------------//
		
		ACK_Flag = PIND & 0x40;	// ACK SIGNAL (PD6)
		
		if(PIND&0x01){		// SWITCH TERMINAL #1 (PD0)
			PORTB |= 0x80;	// DIRECTION SIGNAL (PB7)
			Volt = ((ADC_Read(ADC0)/1023.0)*MAX_VOLT);
			if(Volt < MIN_VOLT)
				Volt = MIN_VOLT;
		}else if(PIND&0x02){	// SWITCH TERMINAL #2 (PD1)
			PORTB &= ~0x80;		// DIRECTION SIGNAL (PB7)
			Volt = ((ADC_Read(ADC0)/1023.0)*MAX_VOLT);
			if(Volt < MIN_VOLT)
				Volt = MIN_VOLT;
		}else{
			Volt = 0;}
			
		C_PHa = (((ADC_Read(ADC1)/1023.0)*AMMETER_VOLT)/RESISTOR_VALUE);
		C_PHb = (((ADC_Read(ADC2)/1023.0)*AMMETER_VOLT)/RESISTOR_VALUE);
		C_PHc = (((ADC_Read(ADC3)/1023.0)*AMMETER_VOLT)/RESISTOR_VALUE);
		
		//------------CHECK FOR CURRENT FAULT------------//
		
		if(C_PHa > CURRENT_THRESHOLD || C_PHb > CURRENT_THRESHOLD || C_PHc > CURRENT_THRESHOLD){
			PORTD |= 0x08;	// FAULT SIGNAL (PD3)
			while(1);		// wait for manual reset
		}
		
		//------------CHECK IF NEW DATA IS RECIEVED------------//
		
		if(Volt == prev_Volt || fabs(Volt-prev_Volt) < 0.1)
		continue;
		
		//------------OUTPUT DATA TO LCD------------//
		
		if(Volt == 0 && !(PIND&0x01) && !(PIND&0x02)){
			LCD_clear();
			LCD_set_cursor(0,4);
			LCD_write_string("Stopped");
		}else{
			LCD_set_cursor(0,0);
			LCD_write_string("Voltage:");
			LCD_set_cursor(1,0);
			LCD_write_string("Frequency: ");
			LCD_set_cursor(0,8);
			LCD_write_float(Volt);
			LCD_write_string(" V");
			LCD_set_cursor(1,11);
			LCD_write_int(90);
			LCD_write_string(" HZ");
		}
		
		//------------SET READY FLAG AND SEND DATA------------//
		
		PORTD |= 0x20;		// READY SIGNAL (PD5)
		PORTC = (Volt*10);	// DATA PORTC
		
		//------------WAIT FOR THE PILOT TO RECIEVE THE DATA------------//
		
		while (ACK_Flag == (PIND&0x40));
		PORTD &= ~0x20;		// READY SIGNAL (PD5)
		prev_Volt = Volt;	
    }
}

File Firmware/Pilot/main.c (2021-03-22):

/** @mainpage About
 *  @author Loay Ashraf <loay.ashraf.96@gmail.com>
 *  @version 1.0.0 
 *
 *  This program is implemented on ATmega128 running 
 *	at 16 MHZ CPU clock; it basically controls output 
 *	of three phase bridge inverter and receives set of
 *	switching parameters from the co-pilot like the 
 *	required voltage, commutation frequency, etc. and
 *	sets the output based on the data received; It
 *	communicates with the co-pilot via parallel bus 
 *	using 8-bit data line, one ACK line and one READY 
 *	line, also it receives direction signal via direct
 *	pin connection and can be interrupted directly by
 *	the co-pilot in case of current overload on any of
 *	the three phases. 
 *	
 *	@pinassignments	
 *	
 *	- PA7: Direction Data signal
 *	- PB5-7: Phases control signal
 *	- PC0-7: Parallel bus 8-bit Data signal
 *	- PD0: Current Overload ERROR signal
 *	- PD5: Parallel bus READY signal
 *	- PD6: Parallel bus ACK signal
 *  
 *	@see main.c
 */

/** @file main.c
 *  @brief includes the main function
 *  
 *  the main function keeps running the SVPWM algorithm
 *	during each iteration of the while loop, sets new
 *	compare register values for the 16-bit timer1 and 
 *	ONLY checks for new data from the co-pilot on the
 *	beginning of new commutation cycle.
 *
 *  @author Loay Ashraf
 *	@version 1.0.0
 *  @pre include SVPWM.h, delay.h and set F_CPU in micro_config.h
 *  @bug no known bugs
 *  @see micro_config.h
 */

//------------INCLUDE SVPWM LIBRARY------------//

#include "SVPWM.h"

//------------DEFINE GLOBAL VARIABLES------------//

/** @var uint16 direction
 *  @brief direction flag (0 for backward, 1 for forward)
 */

uint8 Frequency, theta, theta_step, sector, direction;
uint16 PWM0, PWM1, PWM2;
float Voltage;

/** @brief the main function
 *
 *  see main.c description
 *
 *  @return exit status (1 or 0)
 */
int main(void){
   
   //------------INITIALIZE I/O PORTS------------//
   
   DDRA = 0x00;
   DDRB = 0xE0;
   DDRC = 0x00;
   DDRD = 0x40;
   
   //------------ALIGN ROTOR SHAFT------------//
   
   PORTB |= 0x20;
   _delay_ms(1);
   PORTB &= ~0x20;
   
   //------------WAIT TO RECIEVE DATA------------//
   
   while(!(PIND & 0x20));
   Voltage = (PINC/10.0);
   Frequency = 50;
   theta_step = ((long)360*233*Frequency)/(SW_FREQUENCY*60);	// calculate angle step based on commutation frequency
   direction = ((PINA & 0x80) >> 7);
   PORTD ^= 0x40;
   
   //------------RUN SVPWM CALCULATIONS AND INITIALIZE TIMER------------//
   
   sector = 1;
   theta = 0;
   SVPWM();
   if(direction == FORWARD)
   timer_load(PWM0, PWM1, PWM2);	// forward direction
   else
   timer_load(PWM0, PWM2, PWM1);	// backward direction
   timer_init();
   
	while (1){
		
		//------------CHECK FOR CURRENT FAULT SIGNAL------------//
		
		if(PIND & 0x01){
			shutdown();	
			while(1);	// wait for manual reset	
		}
		
		//------------CHECK FOR NEW DATA AT THE BEGINNING OF THE NEW CYCLE------------//
		
		if(sector == 1 && theta == 0 && PIND & 0x20){
			
			Voltage = (PINC/10.0);
			if(Voltage == 0){
				
				//------------SEND ACK AND SHUTDOWN------------//
				
				PORTD ^= 0x40;
				shutdown();
				
				//------------WAIT TO RECIEVE NEW DATA------------//
				
				while(!(PIND & 0x20));
				Voltage = (PINC/10.0);
				Frequency = 50;
				theta_step = ((long)360*233*Frequency)/(SW_FREQUENCY*60);	// calculate angle step based on commutation frequency
				direction = ((PINA & 0x80) >> 7);
				PORTD ^= 0x40;
				
				//------------REINTIALIZE------------//
				
				PORTB = 0x00;
				SVPWM();
				if(direction == FORWARD)
				timer_load(PWM0, PWM1, PWM2);	// forward direction
				else
				timer_load(PWM0, PWM2, PWM1);	// backward direction
				timer_init();
			}else{	
				Frequency = 50;
				theta_step = (int) 0.2*Frequency;	// calculate angle step based on commutation frequency
				direction = ((PINA & 0x80) >> 7);
				PORTD ^= 0x40;
			}	
		}
		
		//------------RUN SVPWM CALCULATIONS FOR EACH VECTOR AND UPDATE COMPARE REGISTERS------------//
		
		SVPWM();
		while(!(TIFR & (1<<ICF1)));
		if(direction == FORWARD)
		timer_load(PWM0, PWM1, PWM2);	// forward direction
		else
		timer_load(PWM0, PWM2, PWM1);	// backward direction
		TIFR |= (1<<ICF1);				// clear input capture flag

    }
}
